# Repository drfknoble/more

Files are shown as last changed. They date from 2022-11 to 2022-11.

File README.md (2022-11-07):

# My Other Robot for Education (MORE)










## Introduction

Welcome to my repository for my My Other Robot for Education (MORE) project.

<div>
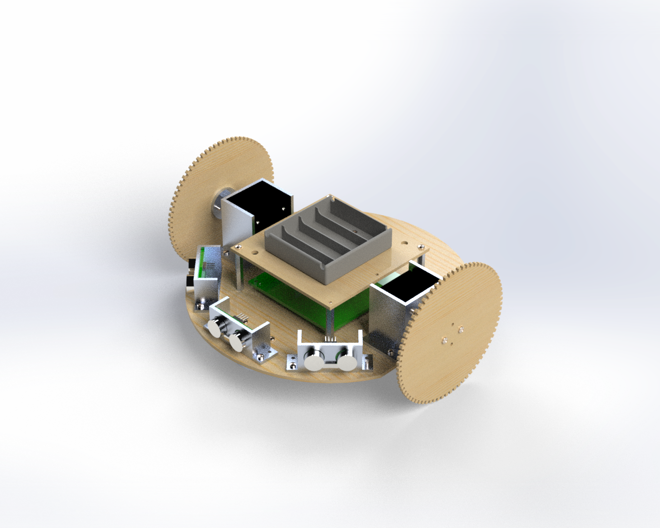
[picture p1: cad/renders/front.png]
    
    
</div>

## Motivation

I started this project after developing my LORE robot (see [http://github.com/DrFKNoble/lore](http://github.com/DrFKNoble/lore)) and seeing how low-cost components affected the robot's performance.

One of the main problems the robot had was that the continuous rotation servo motors I used would start to "drift" after some time (and would need to be manually tuned when they did). So I decided to build a better robot, which used stepper motors instead on servo motors.

## Aims

The aims of this project included:
- Improving upon LORE's performance by using more robust components.
- Developing another mobile robot that, this time, can be used to teach students the principles of mechatronics and robotics.

## Objectives

The objectives of this project included:
- Creating accessible Computer Aided Design (CAD) files.
- Creating accessible Electronics Design Automation (EDA) files.
- Creating accessible source code and software libraries.
- Creating an easy-to-assemble mobile robot that uses an Arduino microcontroller, stepper motors, stepper motor drives, and ultrasonic sensors.

## Repository Structure

The repository is organised as follows:

```console
/MORE      
    /cad                          
        /solidworks                    
        /freecad
        /fabrication
        /renders                     
    /pcb
        /eagle
        /kicad
        /fabrication
    /src
    /doc                      
        /img
        /programming_guide
```

All CAD files can be found in the `/cad` sub-directory. I've included the original SOLIDWORKS files and the open-source equivalents.

All EDA files can be found in the `/pcb` sub-directory. I've included the original Eagle files and the open-source equivalents.

All source code and software libaries are included in the `/src` sub-directory.

Documentation is included in the `/doc` sub-directory.

## Tools Used

I have used the following tools in this project:
- SOLIDWORKS and FreeCAD.
- Eagle and KiCAD.
- Microsoft Visual Studio and Arduino Integrated Development IDE (IDE).

Get FreeCAD here: https://www.freecadweb.org/.  
Get KiCAD here: https://www.kicad.org/.  
Get Arduino IDE here: https://www.arduino.cc/en/software.  
Get Visual Studio here: https://visualstudio.microsoft.com/.  

Alternatively, you can use Microsoft Visual Studio Code as the IDE.

Get Code here: https://code.visualstudio.com/.

## Credit

Dr Frazer K. Noble  
http://drfknoble.com

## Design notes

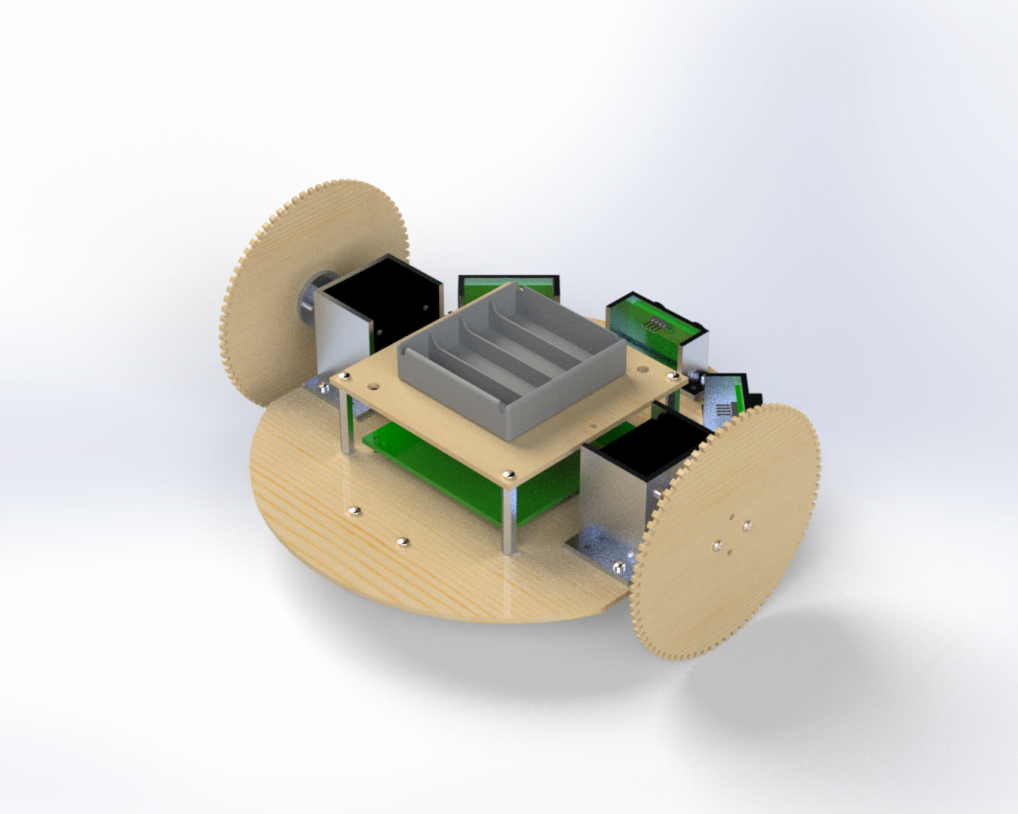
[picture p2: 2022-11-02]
cad/renders/back.png

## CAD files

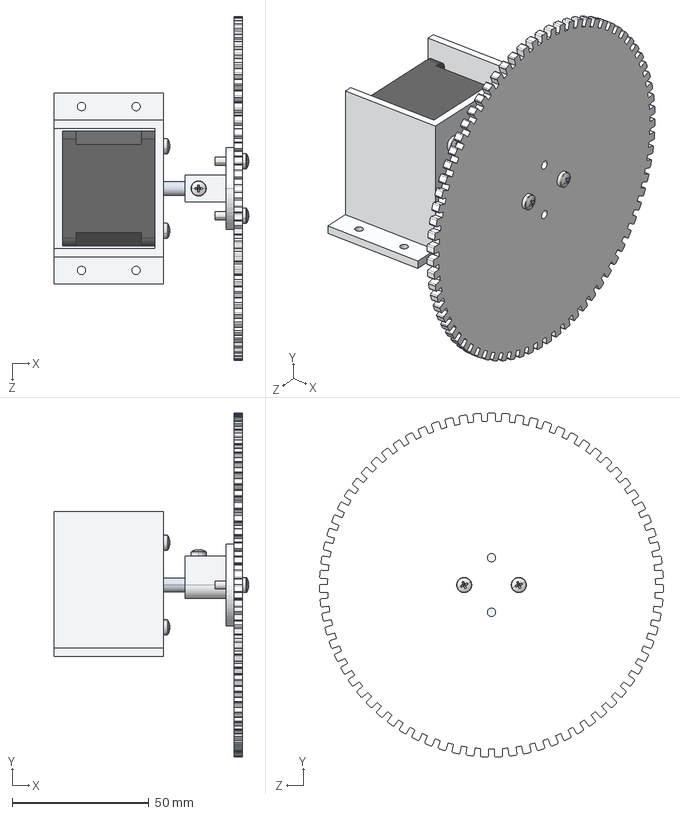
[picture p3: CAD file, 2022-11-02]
cad/freecad/sub_assemblies/motor_assembly.STEP
71.3 x 126.0 x 126.0 mm
motor_bracket
stepper_motor
motor_wheel_coupling
wheel
pan cross head_am_B18.6.7M - M3 x 0.5 x 10 Type I Cross Recessed PHMS --10N x 2
pan cross head_am_B18.6.7M - M3 x 0.5 x 4 Type I Cross Recessed PHMS --4N
pan cross head_am_B18.6.7M - M3 x 0.5 x 5 Type I Cross Recessed PHMS --5N x 4

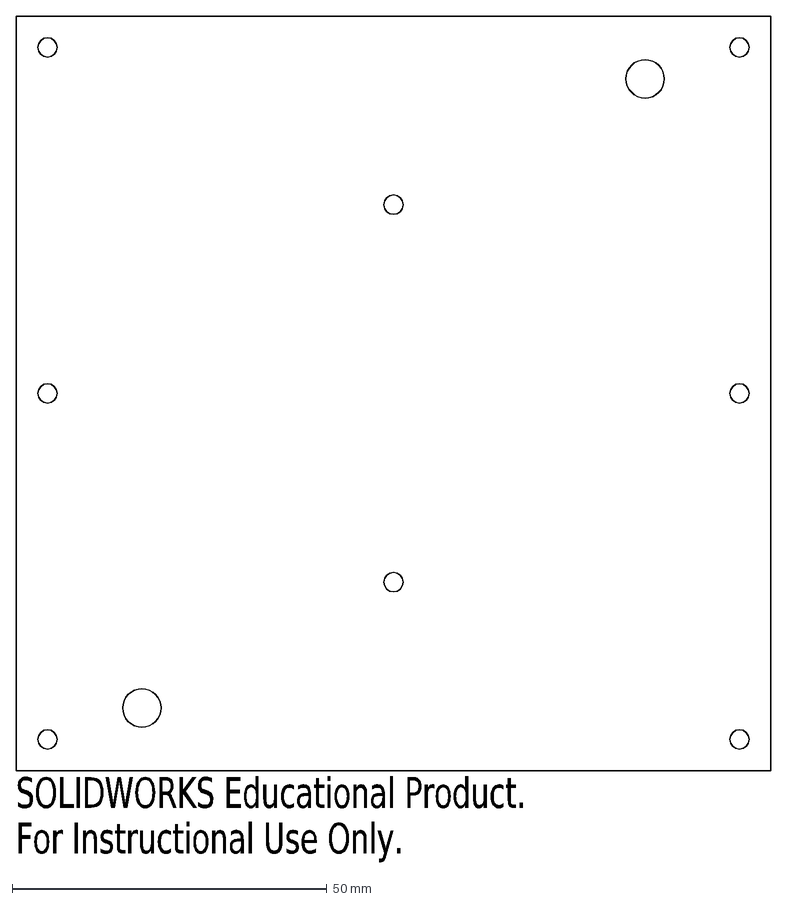
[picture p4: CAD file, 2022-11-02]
cad/fabrication/middle.DXF
SOLIDWORKS Educational Product.
For Instructional Use Only.

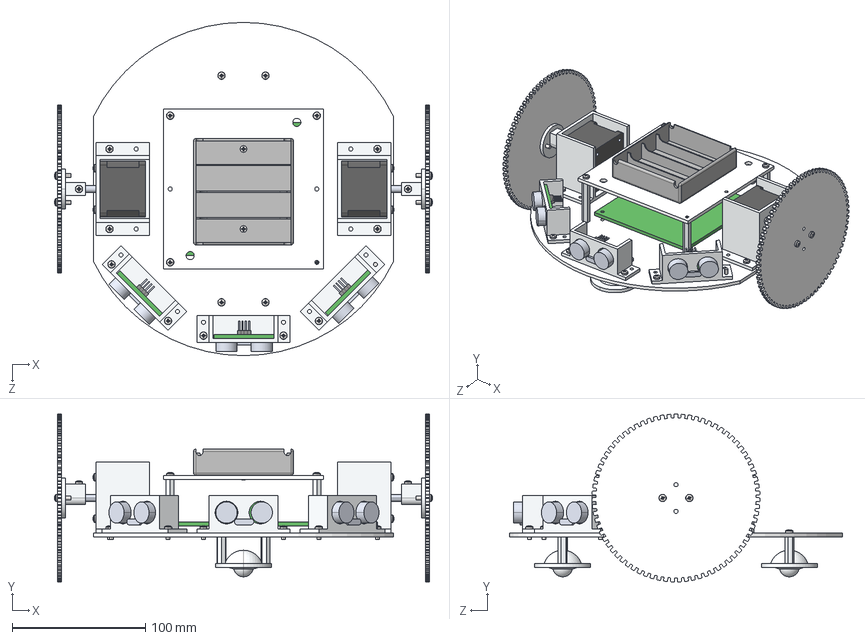
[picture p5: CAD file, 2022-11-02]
cad/freecad/more.STEP
283.6 x 126.0 x 250.0 mm
robot_base
caster x 2
pcb
ultrasonic_bracket x 3
ultrasonic_sensor x 3
battery_holder_base
battery_holder
oval head_am_B18.6.7M - M3 x 0.5 x 5 Type I Cross Recessed OHMS --5N x 2
stand_off_40_mm x 4
stand_off x 4
motor_bracket x 2
stepper_motor x 2
motor_wheel_coupling x 2
wheel x 2
pan cross head_am_B18.6.7M - M3 x 0.5 x 10 Type I Cross Recessed PHMS --10N x 4
pan cross head_am_B18.6.7M - M3 x 0.5 x 4 Type I Cross Recessed PHMS --4N x 2
pan cross head_am_B18.6.7M - M3 x 0.5 x 5 Type I Cross Recessed PHMS --5N x 8
pan cross head_am_B18.6.7M - M3 x 0.5 x 8 Type I Cross Recessed PHMS --8N x 18

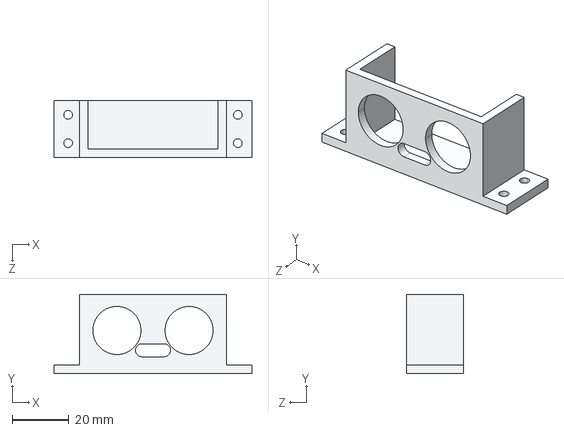
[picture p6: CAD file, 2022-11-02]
cad/freecad/parts/ultrasonic_bracket .STEP
70.0 x 28.0 x 20.0 mm

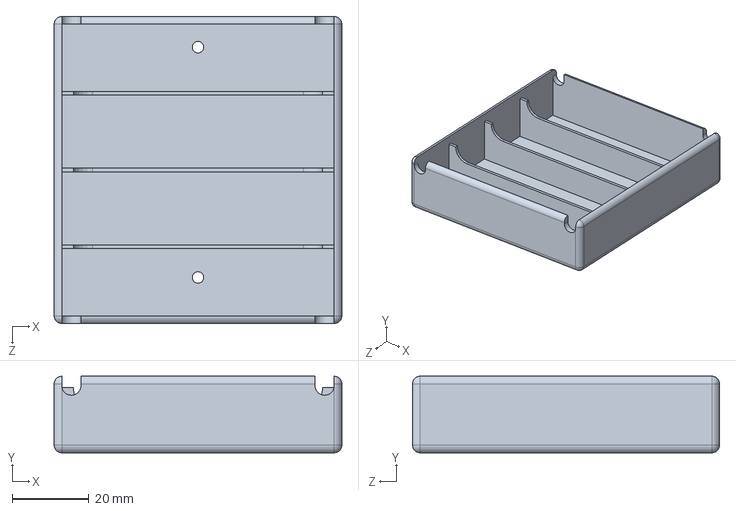
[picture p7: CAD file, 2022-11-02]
cad/solidworks/parts/battery_holder.SLDPRT
75.0 x 20.0 x 80.0 mm

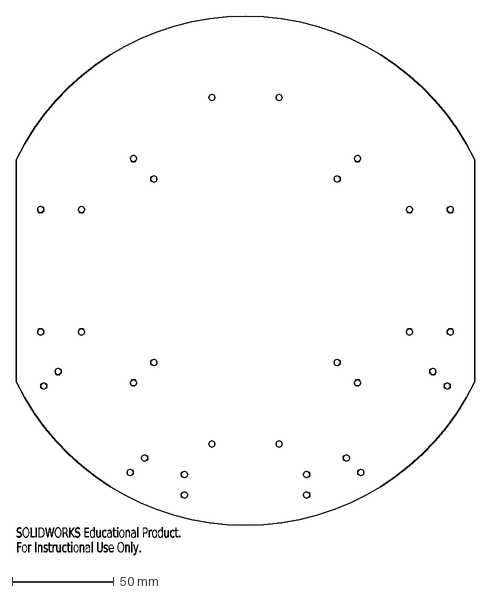
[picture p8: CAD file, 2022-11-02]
cad/fabrication/bottom.DXF
SOLIDWORKS Educational Product.
For Instructional Use Only.

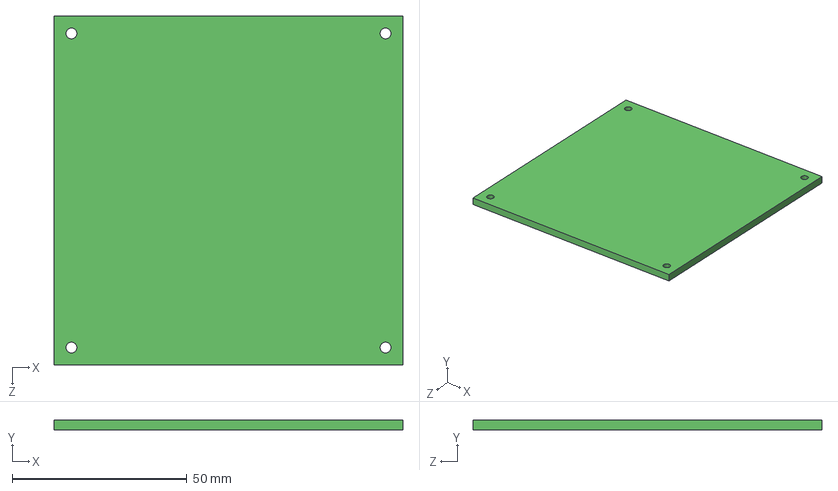
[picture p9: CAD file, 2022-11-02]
cad/freecad/parts/pcb .STEP
100.0 x 3.00 x 100.0 mm

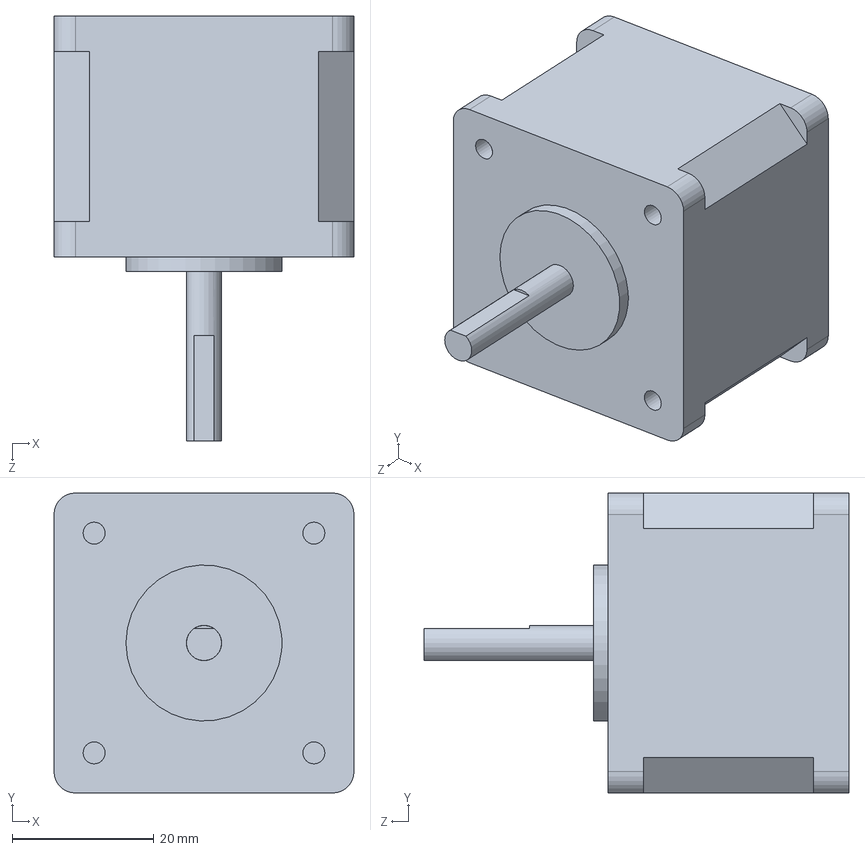
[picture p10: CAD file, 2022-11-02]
cad/solidworks/parts/stepper_motor.SLDPRT
42.3 x 42.3 x 59.9 mm

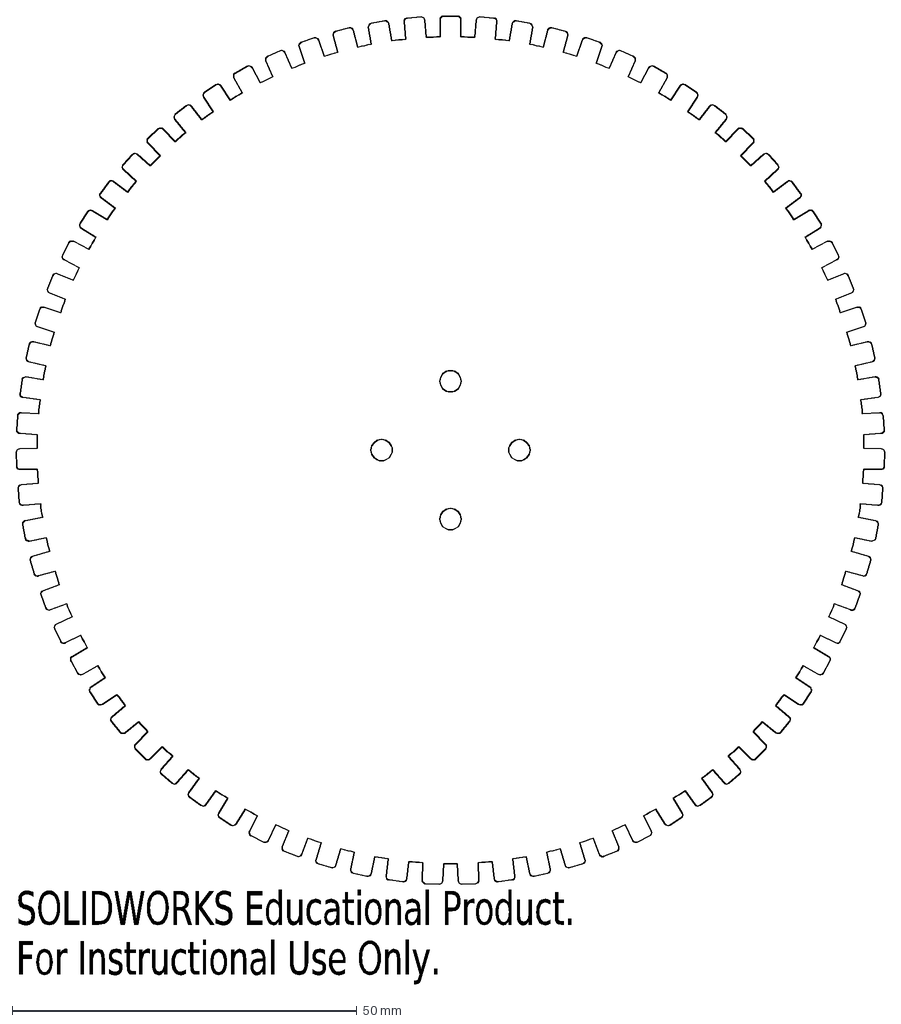
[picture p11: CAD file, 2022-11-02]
cad/fabrication/wheel.DXF
SOLIDWORKS Educational Product.
For Instructional Use Only.

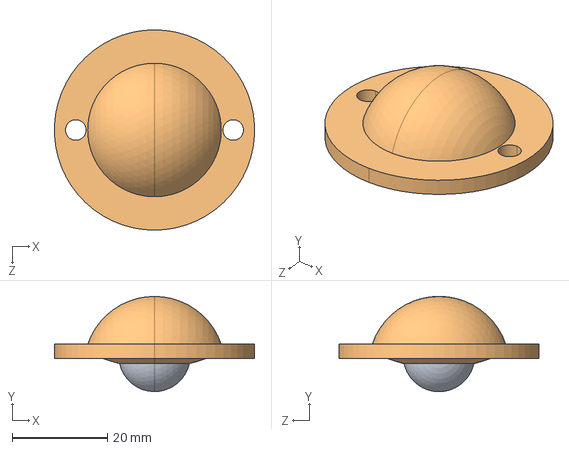
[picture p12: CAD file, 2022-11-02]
cad/freecad/parts/caster.STEP
41.9 x 20.0 x 42.0 mm

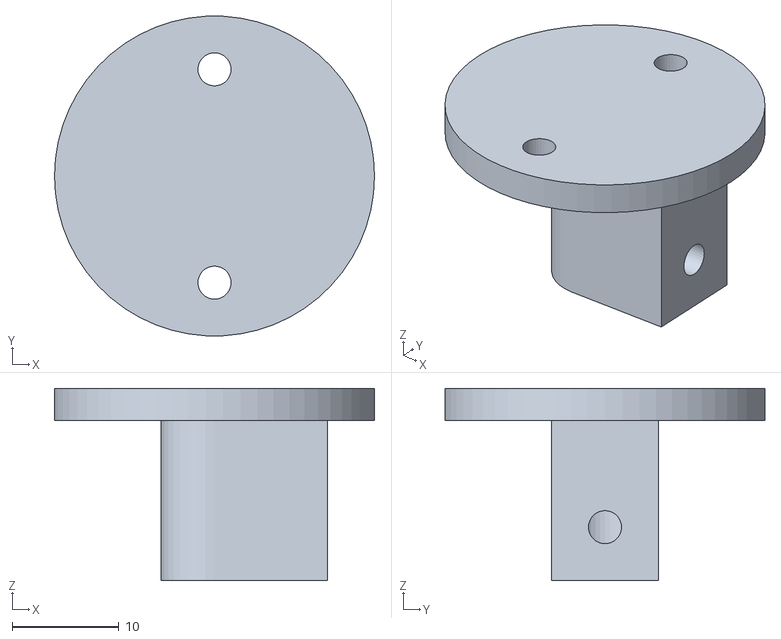
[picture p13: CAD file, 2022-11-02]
cad/fabrication/motor_wheel_coupling.STL
30.0 x 30.0 x 18.0

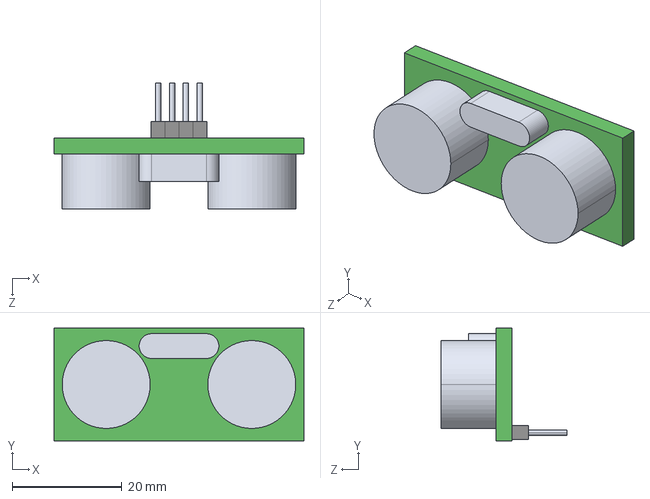
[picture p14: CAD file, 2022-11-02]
cad/freecad/parts/ultrasonic_sensor.STEP
45.5 x 20.5 x 23.0 mm

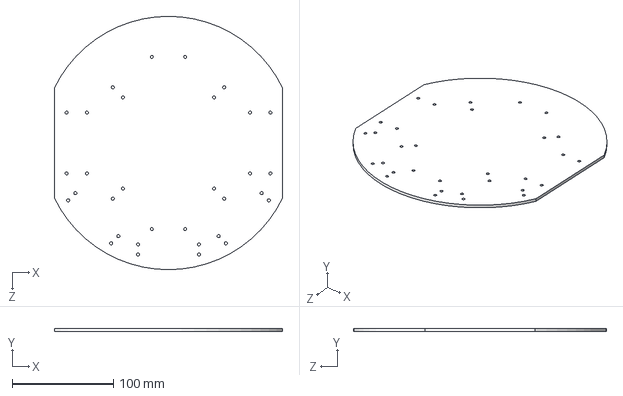
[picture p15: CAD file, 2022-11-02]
cad/freecad/parts/robot_base.STEP
225.0 x 3.00 x 250.0 mm

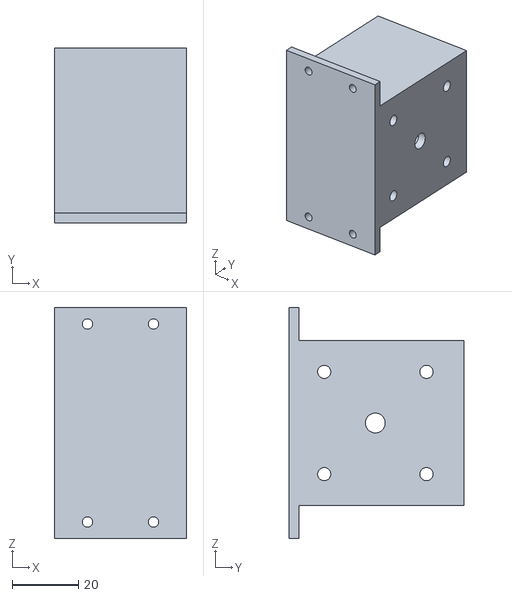
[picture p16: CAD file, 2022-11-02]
cad/fabrication/motor_bracket.STL
40.0 x 53.0 x 70.0

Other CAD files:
cad/fabrication/ultrasonic_bracket.STL
cad/freecad/parts/stand_off.STEP
cad/freecad/parts/motor_wheel_coupling.STEP
cad/freecad/parts/battery_holder_base.STEP
cad/freecad/parts/motor_bracket.STEP
cad/freecad/parts/wheel.STEP
cad/solidworks/more.SLDASM
cad/solidworks/parts/battery_holder_base.SLDPRT
cad/solidworks/parts/caster.SLDPRT
cad/solidworks/parts/motor_bracket.SLDPRT
cad/solidworks/parts/motor_wheel_coupling.SLDPRT
cad/solidworks/parts/pcb .SLDPRT
cad/solidworks/parts/robot_base.SLDPRT
cad/solidworks/parts/stand_off.SLDPRT
cad/solidworks/parts/ultrasonic_bracket.SLDPRT
cad/solidworks/parts/ultrasonic_sensor.SLDPRT
cad/solidworks/parts/wheel.SLDPRT
cad/solidworks/sub_assemblies/motor_assembly.SLDASM

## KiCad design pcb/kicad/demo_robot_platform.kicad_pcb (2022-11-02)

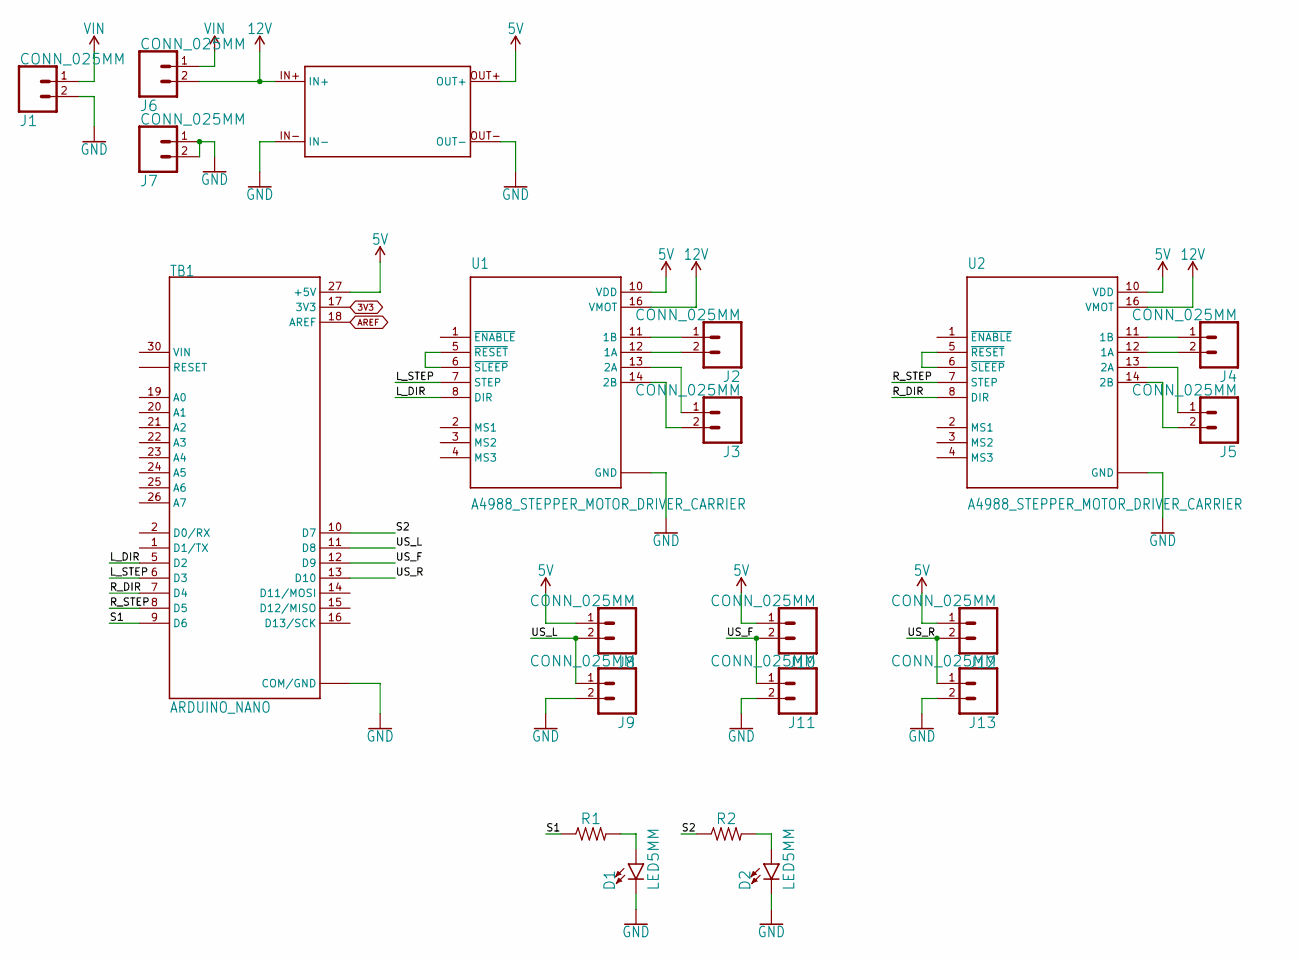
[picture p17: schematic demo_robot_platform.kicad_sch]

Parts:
D1, D2: LED5MM; LED_5MM
J1, J2, J3, J4, J5, J6, J7, J8, J9, J10, J11, J12, J13: CONN_025MM; SCREWTERMINAL-5MM-2
R1, R2: AXIAL-0.3
TB1: ARDUINO_NANO; SHIELD_ARDUINO_NANO
U1, U2: A4988_STEPPER_MOTOR_DRIVER_CARRIER; MODULE_A4988_STEPPER_MOTOR_DRIVER_CARRIER
U$1: DC_DC_CONVERTER

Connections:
3V3: TB1.17 (3V3)
5V: J8.1, J10.1, J12.1, TB1.27 (+5V), U1.10 (VDD), U2.10 (VDD), U$1.OUT+
12V: J6.2, U1.16 (VMOT), U2.16 (VMOT), U$1.IN+
AREF: TB1.18 (AREF)
GND: D1.K (C), D2.K (C), J1.2, J7.1, J7.2, J9.2, J11.2, J13.2, TB1.4 (COM/GND), TB1.29 (COM/GND), U1.9 (GND), U1.15 (GND), U2.9 (GND), U2.15 (GND), U$1.IN-, U$1.OUT-
L_DIR: TB1.5 (D2), U1.8 (DIR)
L_STEP: TB1.6 (D3), U1.7 (STEP)
unnamed: J2.1, U1.11 (1B)
unnamed: J2.2, U1.12 (1A)
unnamed: J3.1, U1.13 (2A)
unnamed: J3.2, U1.14 (2B)
unnamed: J4.1, U2.11 (1B)
unnamed: J4.2, U2.12 (1A)
unnamed: J5.1, U2.13 (2A)
unnamed: J5.2, U2.14 (2B)
unnamed: U1.5 (~RESET), U1.6 (~SLEEP)
unnamed: U2.5 (~RESET), U2.6 (~SLEEP)
unnamed: D1.A, R1.P$2 (2)
unnamed: D2.A, R2.P$2 (2)
R_DIR: TB1.7 (D4), U2.8 (DIR)
R_STEP: TB1.8 (D5), U2.7 (STEP)
S1: R1.P$1 (1), TB1.9 (D6)
S2: R2.P$1 (1), TB1.10 (D7)
US_F: J10.2, J11.1, TB1.12 (D9)
US_L: J8.2, J9.1, TB1.11 (D8)
US_R: J12.2, J13.1, TB1.13 (D10)
VIN: J1.1, J6.1

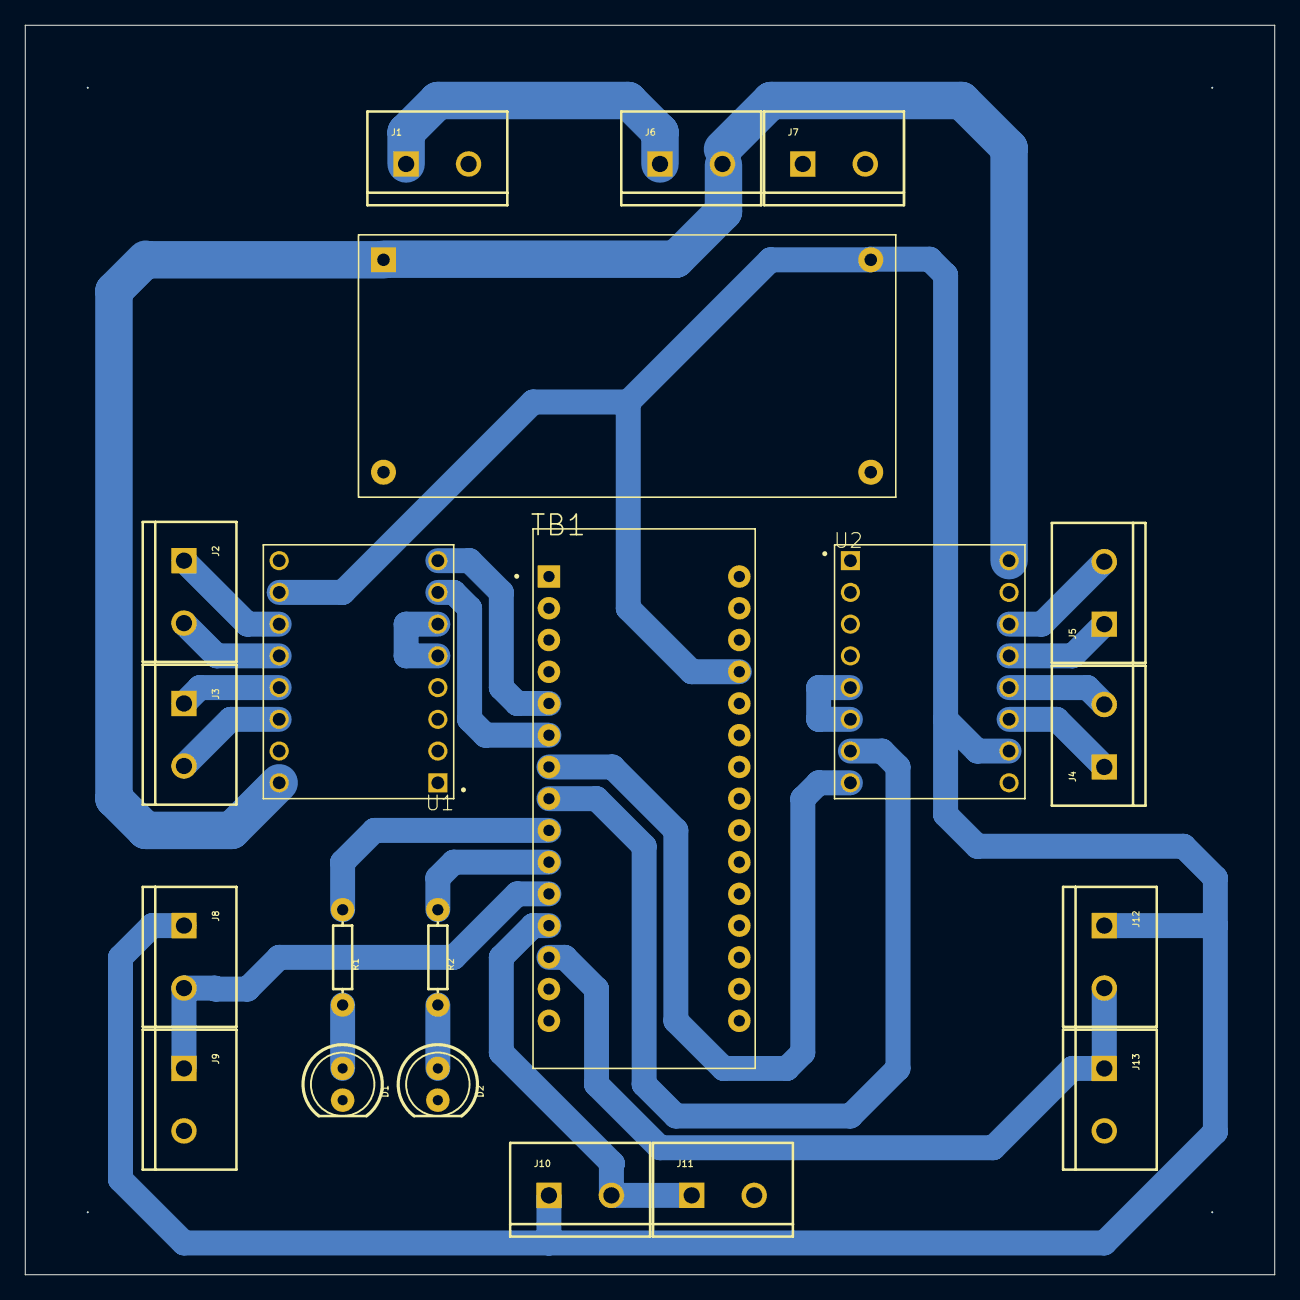
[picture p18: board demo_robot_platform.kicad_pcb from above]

Board: 2 copper layers, 100.0 x 100.0 mm, 25 parts (0 on the bottom side), 25 nets.

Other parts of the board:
@HOLE0, @HOLE1, @HOLE2, @HOLE3: (no value)

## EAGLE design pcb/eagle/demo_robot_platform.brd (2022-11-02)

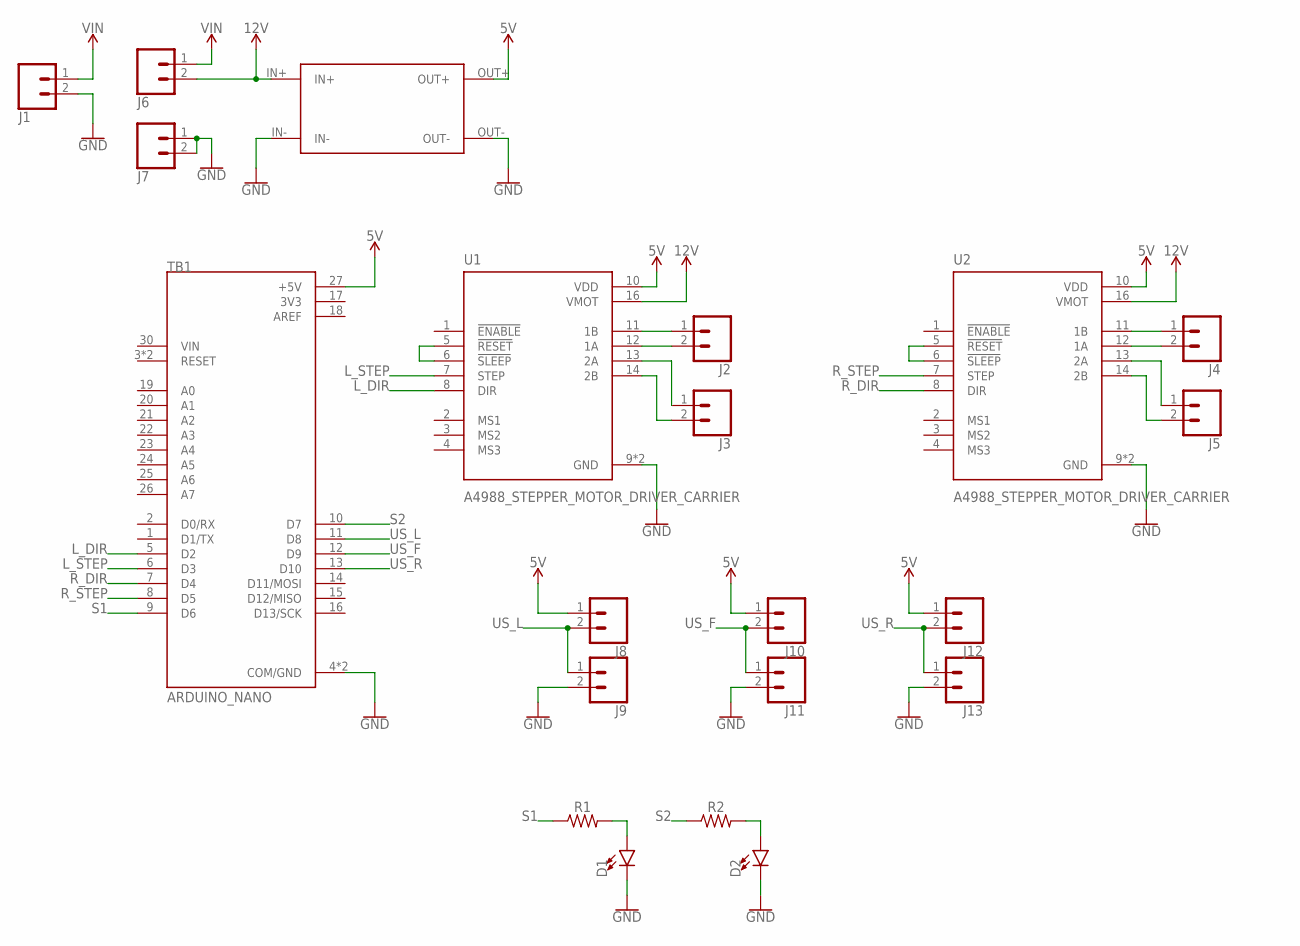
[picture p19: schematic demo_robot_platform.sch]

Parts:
D1, D2: LED5MM; LED_5MM
J1, J2, J3, J4, J5, J6, J7, J8, J9, J10, J11, J12, J13: CONN_025MM; SCREWTERMINAL-5MM-2
R1, R2: AXIAL-0.3
TB1: ARDUINO_NANO; SHIELD_ARDUINO_NANO
U1, U2: A4988_STEPPER_MOTOR_DRIVER_CARRIER; MODULE_A4988_STEPPER_MOTOR_DRIVER_CARRIER
U$1: DC_DC_CONVERTER

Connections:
3V3: TB1.17 (3V3)
5V: J8.1, J10.1, J12.1, TB1.27 (+5V), U1.10 (VDD), U2.10 (VDD), U$1.OUT+
12V: J6.2, U1.16 (VMOT), U2.16 (VMOT), U$1.IN+
AREF: TB1.18 (AREF)
GND: D1.K (C), D2.K (C), J1.2, J7.1, J7.2, J9.2, J11.2, J13.2, TB1.4 (COM/GND), TB1.29 (COM/GND), U1.9 (GND), U1.15 (GND), U2.9 (GND), U2.15 (GND), U$1.IN-, U$1.OUT-
L_DIR: TB1.5 (D2), U1.8 (DIR)
L_STEP: TB1.6 (D3), U1.7 (STEP)
unnamed: J2.1, U1.11 (1B)
unnamed: J2.2, U1.12 (1A)
unnamed: J3.1, U1.13 (2A)
unnamed: J3.2, U1.14 (2B)
unnamed: J4.1, U2.11 (1B)
unnamed: J4.2, U2.12 (1A)
unnamed: J5.1, U2.13 (2A)
unnamed: J5.2, U2.14 (2B)
unnamed: U1.5 (!RESET), U1.6 (!SLEEP)
unnamed: U2.5 (!RESET), U2.6 (!SLEEP)
unnamed: D1.A, R1.P$2 (2)
unnamed: D2.A, R2.P$2 (2)
R_DIR: TB1.7 (D4), U2.8 (DIR)
R_STEP: TB1.8 (D5), U2.7 (STEP)
S1: R1.P$1 (1), TB1.9 (D6)
S2: R2.P$1 (1), TB1.10 (D7)
US_F: J10.2, J11.1, TB1.12 (D9)
US_L: J8.2, J9.1, TB1.11 (D8)
US_R: J12.2, J13.1, TB1.13 (D10)
VIN: J1.1, J6.1

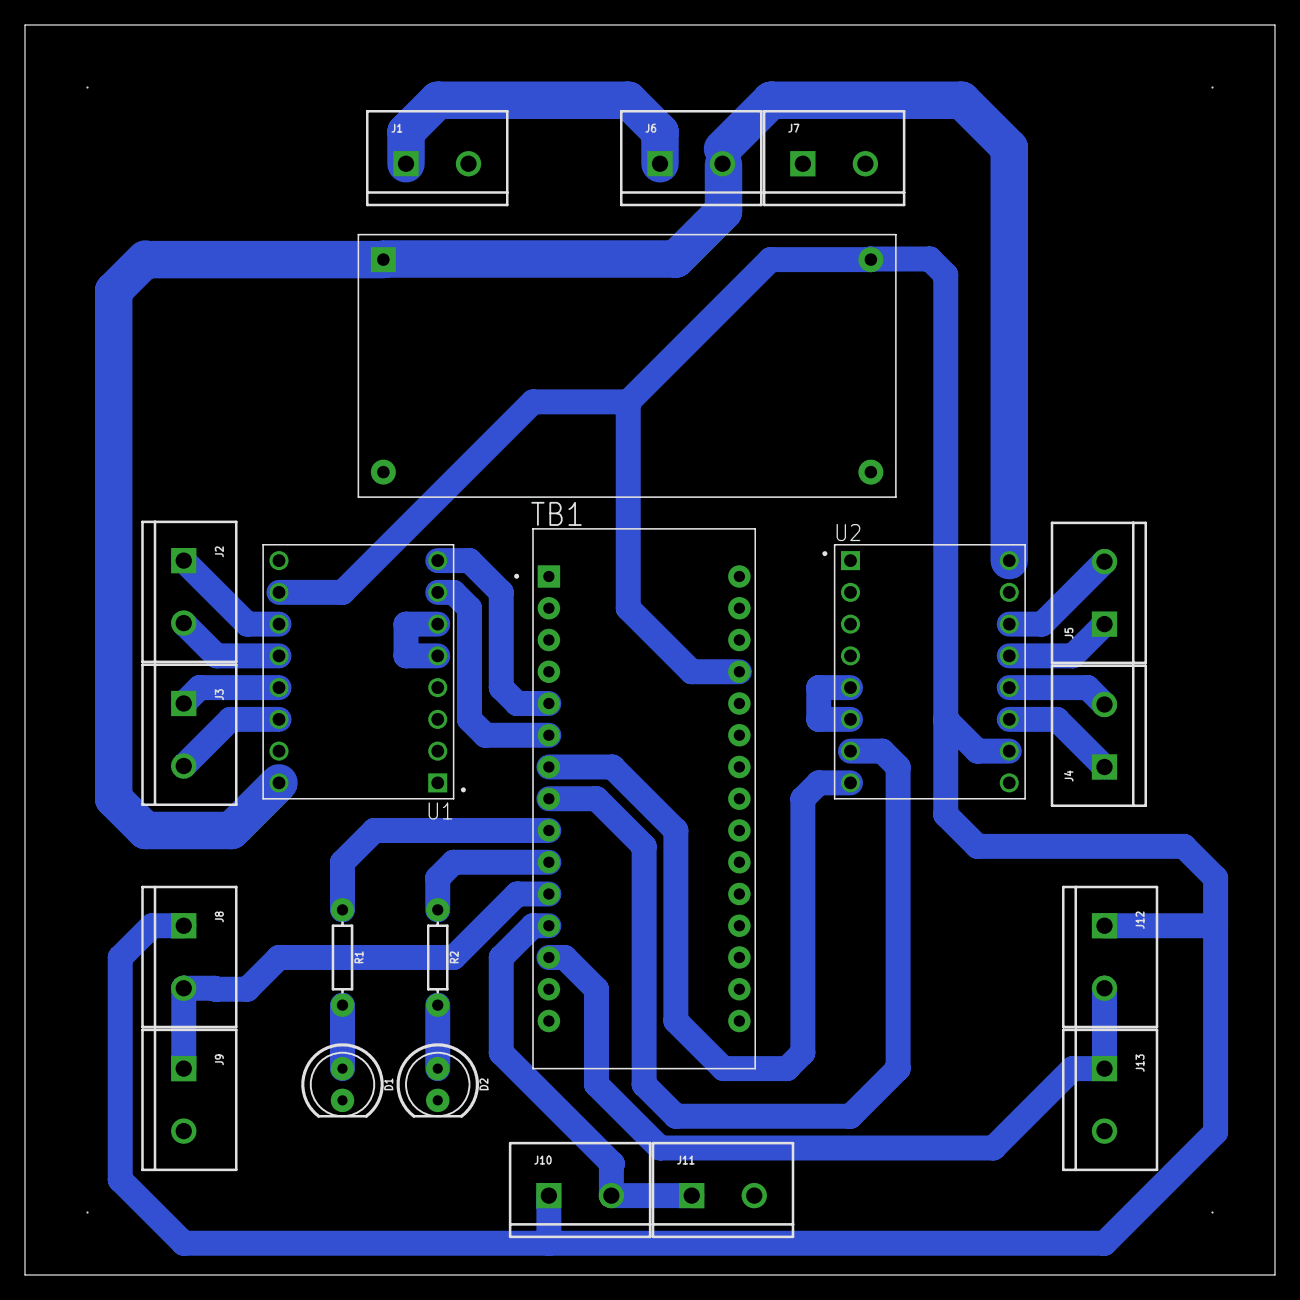
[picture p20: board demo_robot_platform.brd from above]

Board: 2 copper layers, 100.0 x 100.0 mm, 21 parts (0 on the bottom side), 25 nets.

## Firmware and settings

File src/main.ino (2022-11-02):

/*Example sketch to control a stepper motor with A4988 stepper motor driver and Arduino without a library. More info: https://www.makerguides.com */

// Define stepper motor connections and steps per revolution:
int dirPinLeft = 2;
int stepPinLeft = 3;
int dirPinRight = 4;
int stepPinRight = 5;
int stepsPerRevolution = 200;

int statusLED1 = 6;
int statusLED2 = 7;
int sensorFront = 9;
float frontDuration = 0.0;
float frontDistance = 5000.00;

bool completed = false;

void forward(float distance = 250.0) {

//  int count = 5;
//  float sum = 0.0;
//
//  for (int i = 0; i < count; i++) {
// 
//    sum += frontSensor();
//
//  }
//
//  frontDistance = (sum / count);
//
//  if (frontDistance < distance) {
//    return;
//  }
//    
  
  digitalWrite(dirPinLeft, LOW);
  digitalWrite(dirPinRight, LOW);

  float steps = distance / 377.0 * stepsPerRevolution;
 
  for (int i = 0; i < int(steps); i++) {    
    digitalWrite(stepPinLeft, HIGH);
    digitalWrite(stepPinRight, HIGH);
    delayMicroseconds(5000);
    digitalWrite(stepPinLeft, LOW);
    digitalWrite(stepPinRight, LOW);
    delayMicroseconds(5000);
  }

  return;
}

void backward(float distance = 250.0) {
  digitalWrite(dirPinLeft, HIGH);
  digitalWrite(dirPinRight, HIGH);

  float steps = distance / 377.0 * stepsPerRevolution;

  for (int i = 0; i < int(steps); i++) {     
    digitalWrite(stepPinLeft, HIGH);
    digitalWrite(stepPinRight, HIGH);
    delayMicroseconds(5000);
    digitalWrite(stepPinLeft, LOW);
    digitalWrite(stepPinRight, LOW);
    delayMicroseconds(5000);
  }

  return;
}

void right(float angle = 90) {
  digitalWrite(dirPinLeft, HIGH);
  digitalWrite(dirPinRight, LOW);

  float steps = angle * 3.14159 / 180.0 * 135.0 / 377.0 * stepsPerRevolution;

  for (int i = 0; i < int(steps); i++) {
    digitalWrite(stepPinLeft, HIGH);
    digitalWrite(stepPinRight, HIGH);
    delayMicroseconds(5000);
    digitalWrite(stepPinLeft, LOW);
    digitalWrite(stepPinRight, LOW);
    delayMicroseconds(5000);
  }

  return;
}

void left(float angle = 90) {
  digitalWrite(dirPinLeft, LOW);
  digitalWrite(dirPinRight, HIGH);

  float steps = angle * 3.14159 / 180.0 * 135.0 / 377.0 * stepsPerRevolution;

  for (int i = 0; i < int(steps); i++) {
    digitalWrite(stepPinLeft, HIGH);
    digitalWrite(stepPinRight, HIGH);
    delayMicroseconds(5000);
    digitalWrite(stepPinLeft, LOW);
    digitalWrite(stepPinRight, LOW);
    delayMicroseconds(5000);
  }

  return;
}

float frontSensor() {
  float duration = 0.0;
  float distance = 0.0;
  
  pinMode(sensorFront, OUTPUT);
  digitalWrite(sensorFront, LOW);
  delayMicroseconds(2);
  
  digitalWrite(sensorFront, HIGH);
  delayMicroseconds(10);
  digitalWrite(sensorFront, LOW);
  
  pinMode(sensorFront, INPUT);
  duration = pulseIn(sensorFront, HIGH);
  
//  distance = duration * 0.034 / 2; //cm
  distance = 10 * duration * 0.034 / 2; //mm
  
  return distance;
}

void setup() {
  // Declare pins as output:
  pinMode(stepPinLeft, OUTPUT);
  pinMode(dirPinLeft, OUTPUT);
  pinMode(stepPinRight, OUTPUT);
  pinMode(dirPinRight, OUTPUT);

  pinMode(statusLED1, OUTPUT);  
  pinMode(statusLED2, OUTPUT);
  pinMode(sensorFront, OUTPUT);

  digitalWrite(statusLED1, LOW);
  digitalWrite(statusLED2, LOW);
  digitalWrite(sensorFront, LOW);

  Serial.begin(115200);
}

void loop() {

  if (completed == false) {
  
    for (int i = 0; i < 3; i++) {
      forward(1000);
      delay(250);
      left();
      delay(250);
      forward(1000);
      delay(250);
      right();
      delay(250);
    }
  
    completed = true;

  }
    
  int count = 5;
  float sum = 0.0;

  for (int i = 0; i < count; i++) {
 
    sum += frontSensor();

  }

  frontDistance = (sum / count);

  Serial.print("front sensor distance = ");
  Serial.print(frontDistance);
  Serial.println(" mm");

  if (frontDistance <= 500) {
    digitalWrite(statusLED1, HIGH);
    digitalWrite(statusLED2, HIGH);
  } else {
    digitalWrite(statusLED1, LOW);
    digitalWrite(statusLED2, LOW);
  }
}

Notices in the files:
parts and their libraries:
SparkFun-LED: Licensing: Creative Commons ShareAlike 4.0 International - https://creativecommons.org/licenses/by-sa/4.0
